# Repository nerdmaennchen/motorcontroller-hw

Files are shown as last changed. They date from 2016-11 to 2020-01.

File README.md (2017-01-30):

A somewhat easy to build two-layer PCB to controll BLDC-motors with.

The board is designed to have:
	- USB connection (every computer has a USB port but there are virtually no boards out there that offer a USB connection (without an FTDI in between))
	- up to 200W (tested) output power (theoretical -- when ignoring trace resistances -- maximum 900W)
	- digital Hall-Encoder interface
	- analog/absolute hall-encoder interface
	- BEMF measurement for hall-less operation
	- serial interface to cascade multiple BLDC-drivers over one USB interface
	- two PWM outputs for RC-servo motors
	- one connector to attach WS2812b LEDs
	- a layout that allows somewhat easy manufacturing by placing most parts on one layer (I've once built 15 pieces in 8h by hand soldering)
	
The board has four power domains:
	- internal 3.3V -- to power the microcontroller
	- USB-5V -- can power the internal 3.3V domain; protected from the external 5V domain with a diode thus protecting the USB-host from voltage spikes on the external 5V-domain
	- external 5V -- can power the internal 3.3V domain; powers the WS2812b LEDs and RC-servo motors

The board utilizes an STM32F401xx processor which is super nice to program, debug and due to its QFN48 footprint super easy to solder by hand -- as long as you have access to a rework station.
Software for the uC can be found here: https://github.com/nerdmaennchen/motorcontroller-uc-sw
Software for the USB-Host here: https://github.com/nerdmaennchen/motorcontroller-sw

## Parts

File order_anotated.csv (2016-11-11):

Qty | Value | Footprint
12 | 2.2uF | Capacitors_SMD:C_0603
12 | 1276-6592-1-ND
3 | 10nF | Capacitors_SMD:C_0603
3 | 1276-1921-1-ND
1 | 22nF | Capacitors_SMD:C_0603
1 | 490-3169-1-ND
3 | 100nF | Capacitors_SMD:C_0603
3 | 1276-1258-1-ND
1 | 4.7uF | Capacitors_SMD:C_0805
2 | 22pF | Capacitors_SMD:C_0603
2 | 1276-2227-1-ND
1 | status | LEDs:LED_0805
1 | 160-1434-1-ND
2 | D_Schottky | Diodes_SMD:SOD-323
2 | NSR0530HT1GOSCT-ND
4 | 3.3V | Diodes_SMD:SOD-323
4 | MM3Z3V3T1GOSCT-ND
1 | USB_OTG | Connect:USB_Micro-B
1 | 609-4618-1-ND
1 | CONN_01X03 | Terminal_Blocks:TerminalBlock_Pheonix_MPT-2.54mm_3pol
1 | ED10562-ND
1 | CON_PWR_BRD | Terminal_Blocks:TerminalBlock_Pheonix_MPT-2.54mm_4pol
1 | ED10563-ND
1 | CON_HALL | Terminal_Blocks:TerminalBlock_Pheonix_MPT-2.54mm_5pol
1 | ED10564-ND
6 | Q_NMOS_DGS | BLDC:SOT1210
6 | 568-13008-1-ND
1 | 2N7002 | TO_SOT_Packages_SMD:SOT-23
1 | 2N7002ECT-ND
1 | 330 | Resistors_SMD:R_0603
1 | 311-330GRCT-ND
4 | 10kR | Resistors_SMD:R_0603
4 | 311-10KGRCT-ND
1 | 1R | Resistors_SMD:R_0603
1 | 1276-4991-1-ND
6 | 10R | Resistors_SMD:R_0603
6 | 311-10KGRCT-ND
1 | 0R/50kR | Resistors_SMD:R_0603
1 | NA/50kR | Resistors_SMD:R_0603
1 | 311-47KGRCT-ND
2 | .01 | Resistors_SMD:R_1210
2 | 1276-6160-1-ND
1 | 33k | Resistors_SMD:R_Array_Concave_4x0603
1 | 742C083333JPCT-ND
1 | 1k | Resistors_SMD:R_Array_Concave_4x0603
1 | 742C083102JPCT-ND
1 | 10k | Resistors_SMD:R_Array_Concave_4x0603
1 | 742C083103JPCT-ND
1 | STM32F401CBUx | Housings_DFN_QFN:QFN-48-1EP_7x7mm_Pitch0.5mm
1 | LD1117S33TR | TO_SOT_Packages_SMD:SOT-223
1 | 497-1242-1-ND
1 | DRV8303 | BLDC:SOIC-48
1 | 296-40070-1-ND
1 | Crystal | Crystals:Crystal_SMD_5032_2Pads
1 | 535-10630-1-ND
Title
Date
Generated | Di 08 Nov 2016 14:40:50 CET
Total Parts | 76
Total Unique Parts | 37

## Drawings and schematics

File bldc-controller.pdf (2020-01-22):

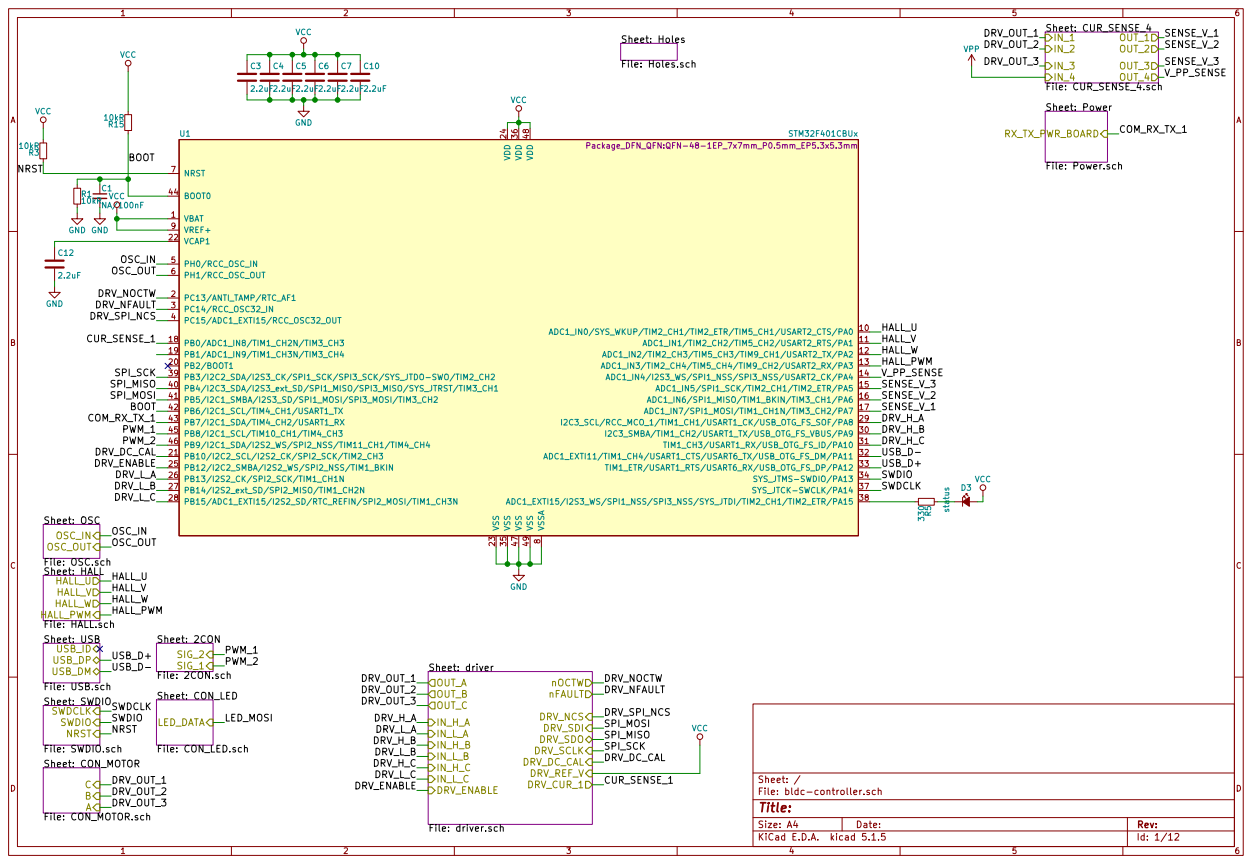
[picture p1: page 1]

Sheet: Holes File: Holes.sch Sheet: OSC

Sheet: Power File: Power.sch RX_TX_PWR_BOARD

Sheet: driver File: driver.sch OUT_A

SWDCLK SWDIO NRST

LED_DATA

Id: 1/12 Title: File: bldc-controller.sch Sheet: /

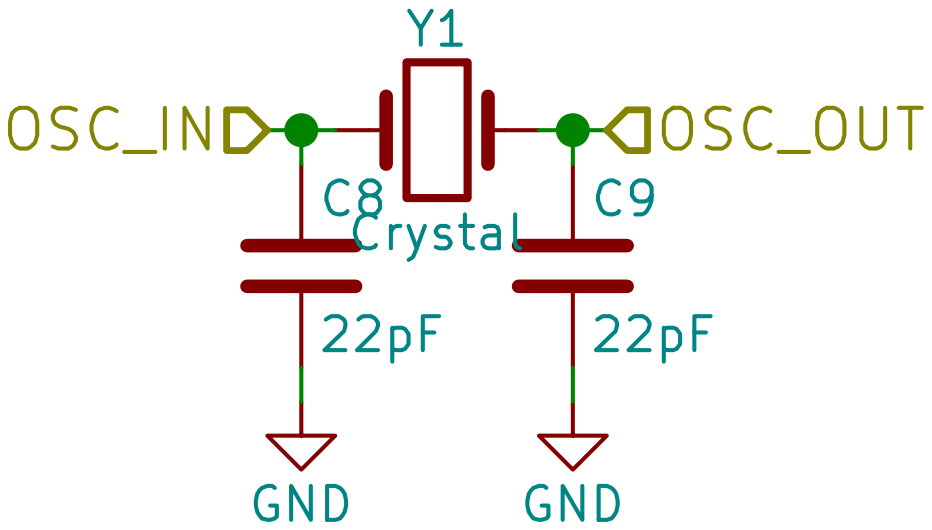
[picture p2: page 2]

Id: 2/12 Title: File: OSC.sch Sheet: /OSC/

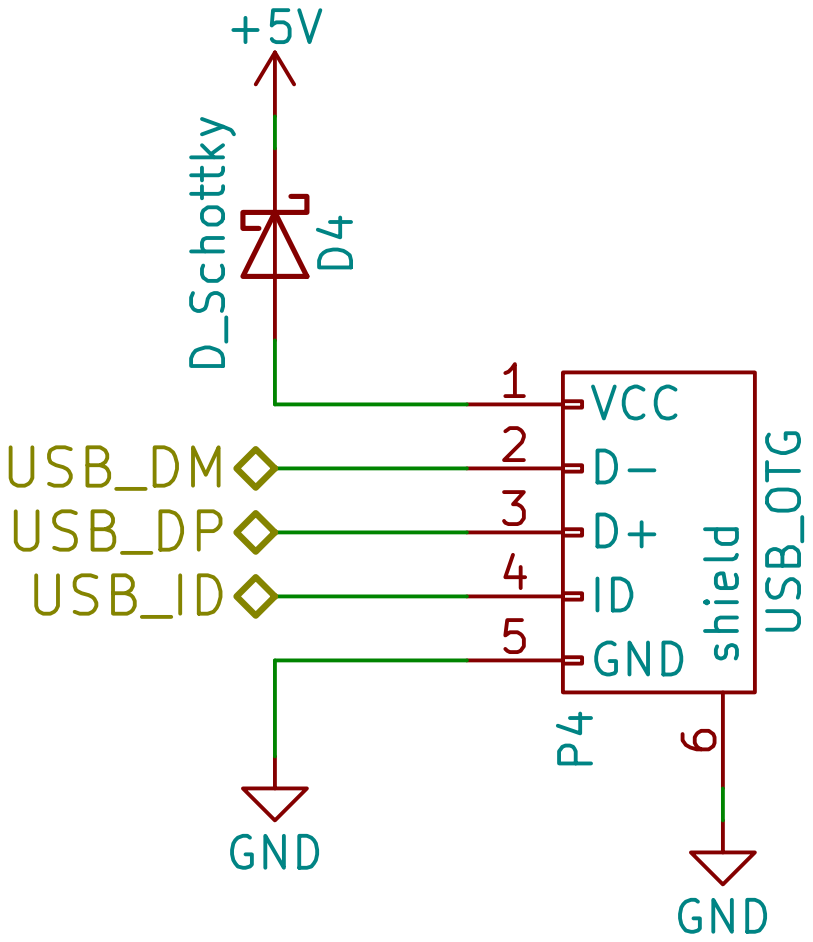
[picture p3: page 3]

Id: 3/12 Title: DreErolf File: USB.sch Sheet: /USB/ +5V

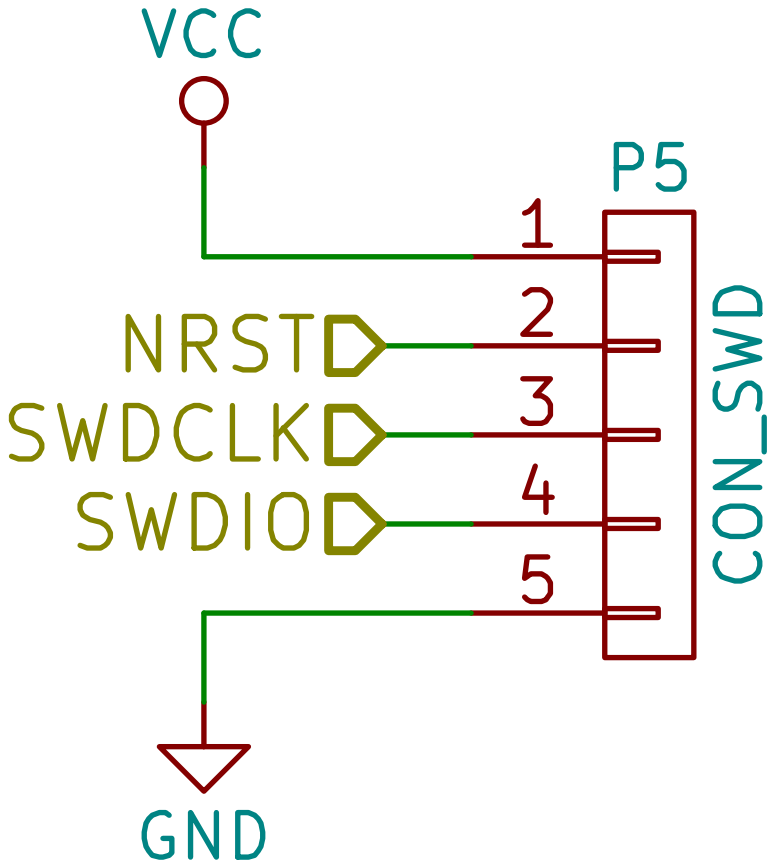
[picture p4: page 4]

Id: 4/12 Title: DreErolf File: SWDIO.sch Sheet: /SWDIO/ GND

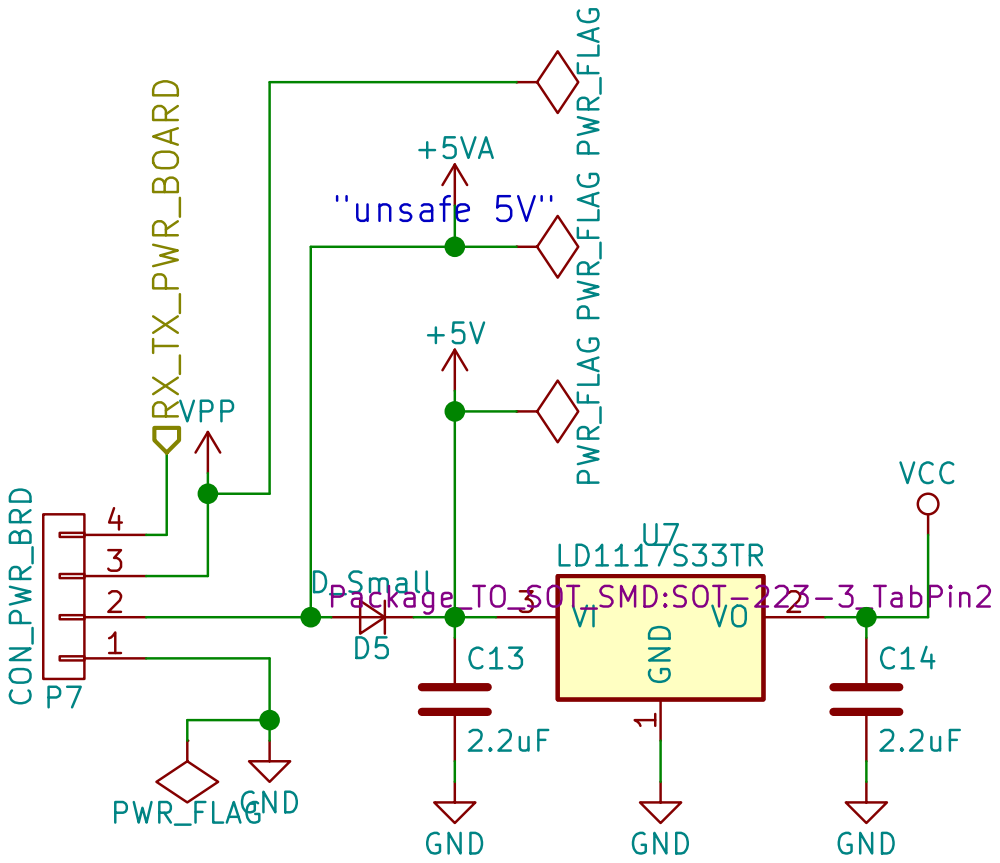
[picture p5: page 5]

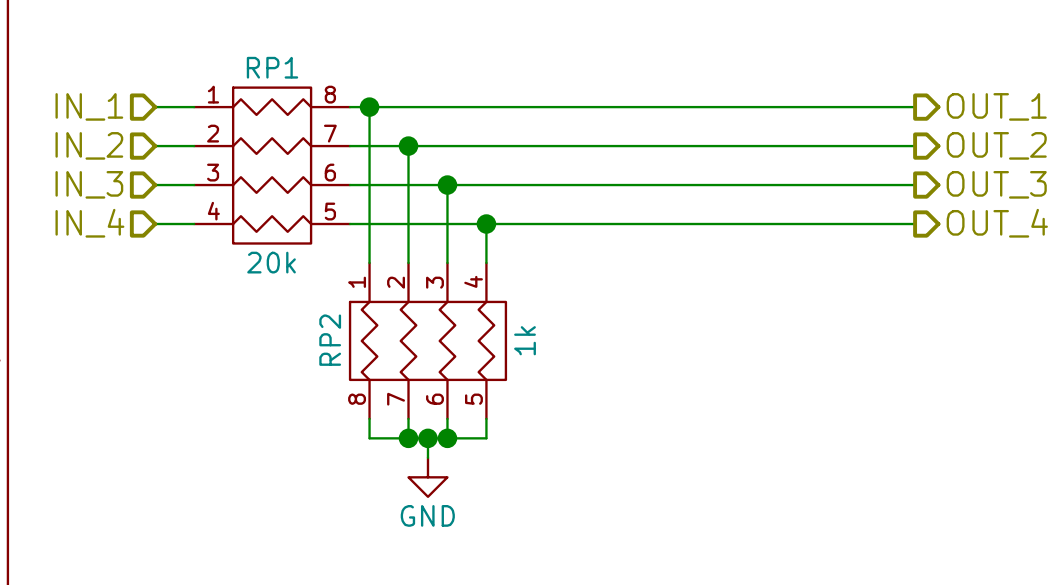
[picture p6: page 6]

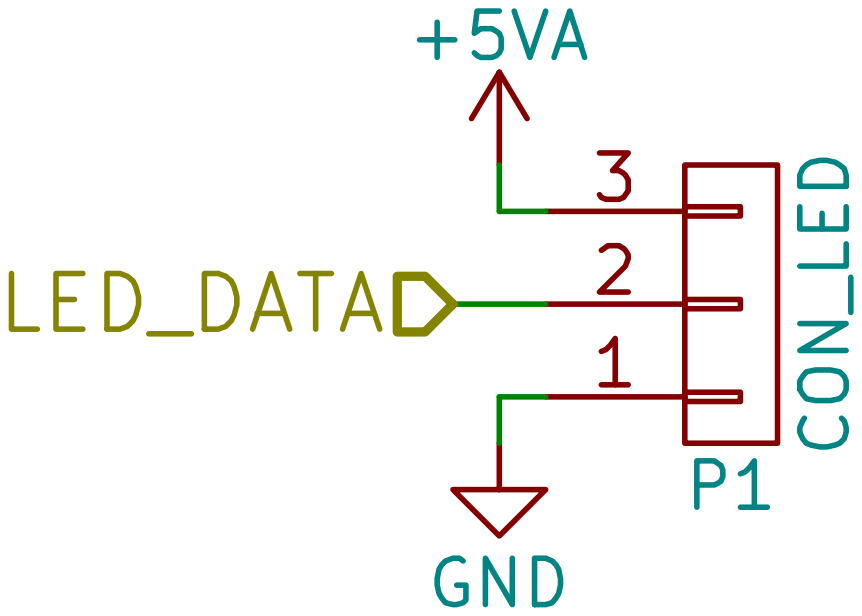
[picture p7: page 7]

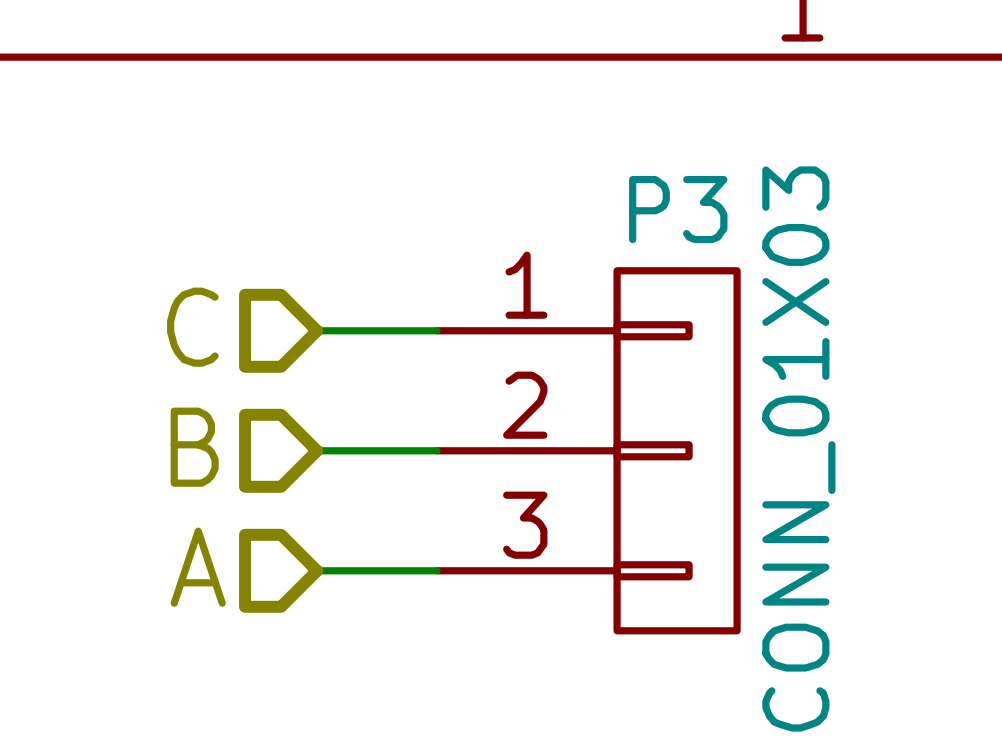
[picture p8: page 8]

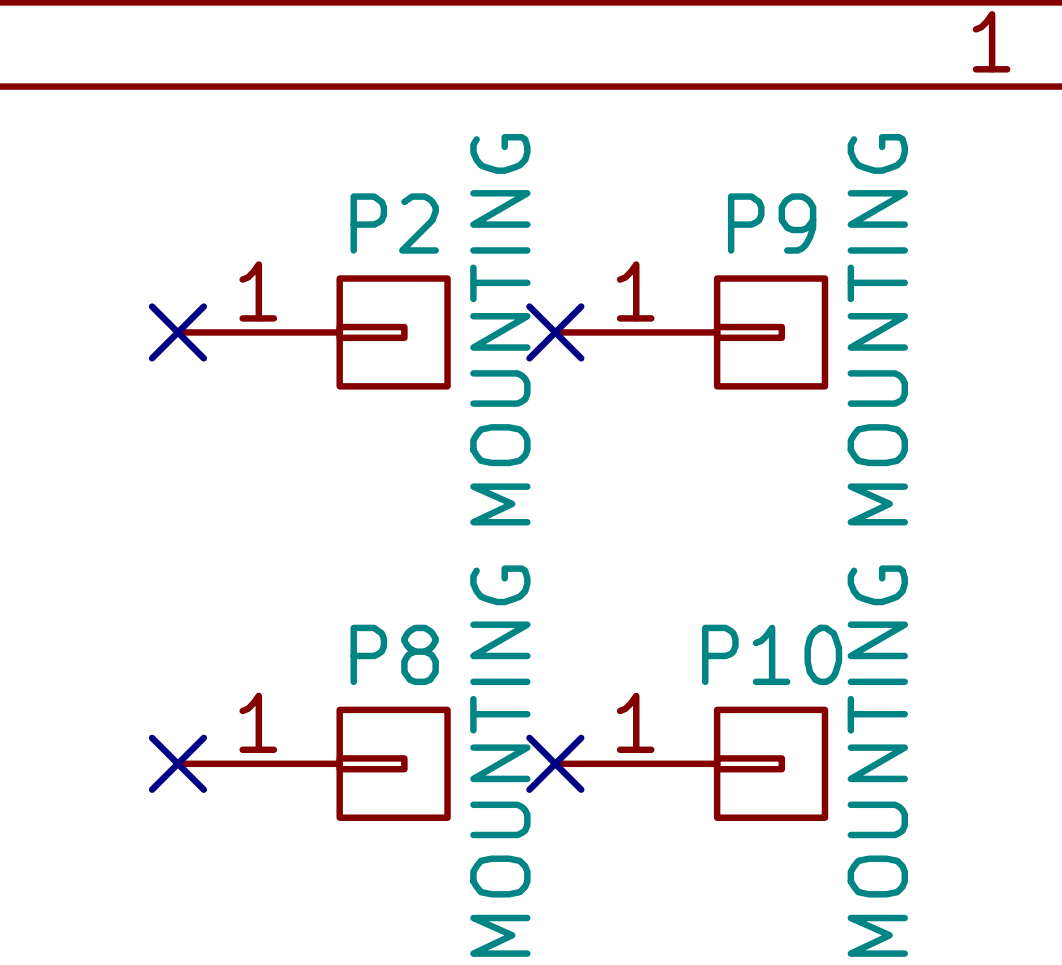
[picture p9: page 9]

Id: 9/12 Title: File: Holes.sch Sheet: /Holes/ 1 P2 MOUNTING 1 P9 MOUNTING 1 P8 MOUNTING 1 P10 MOUNTING

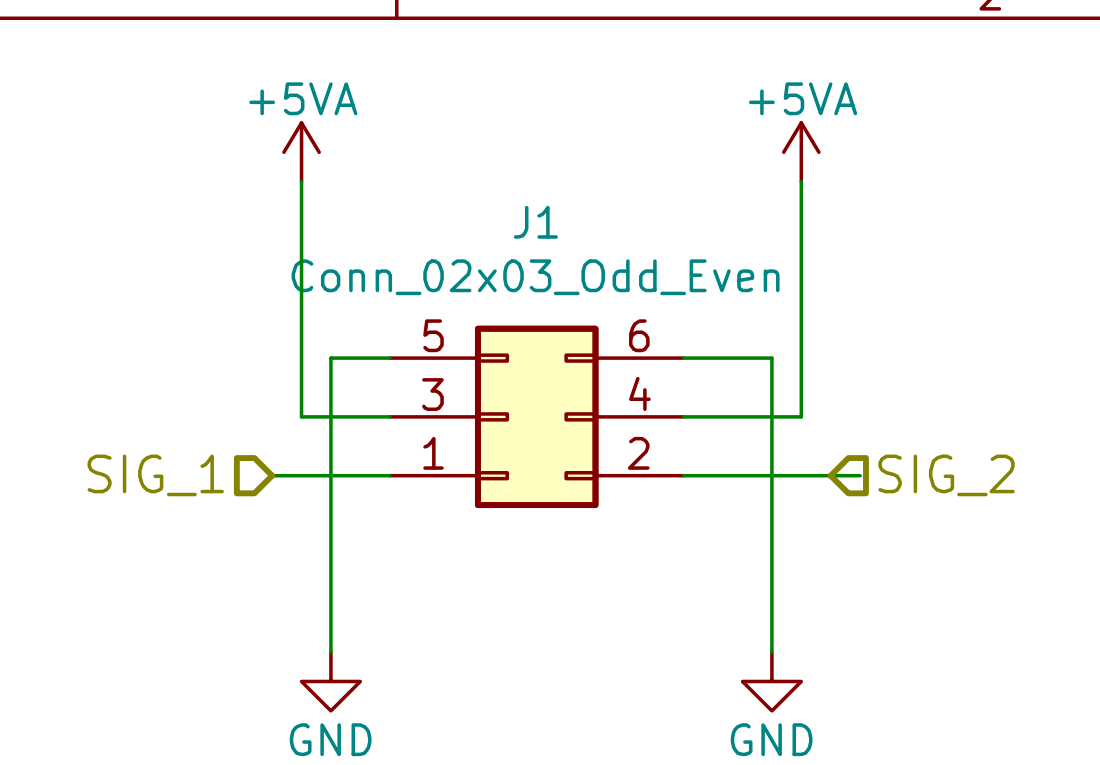
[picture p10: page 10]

Id: 10/12 Title: File: 2CON.sch Sheet: /2CON/

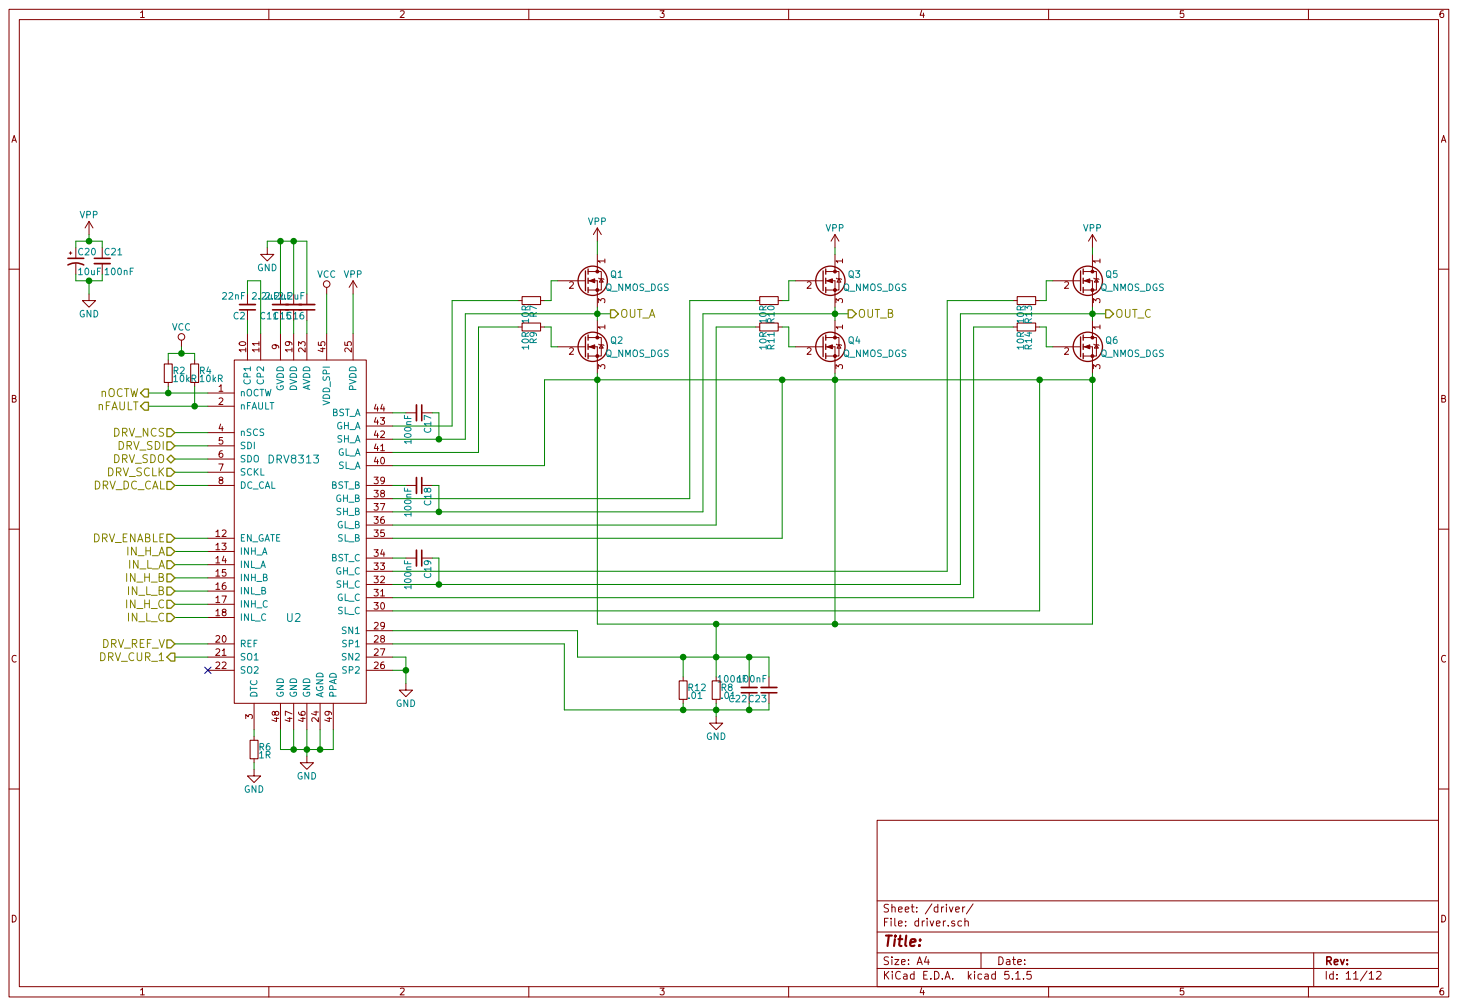
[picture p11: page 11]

Id: 11/12 Title: File: driver.sch Sheet: /driver/

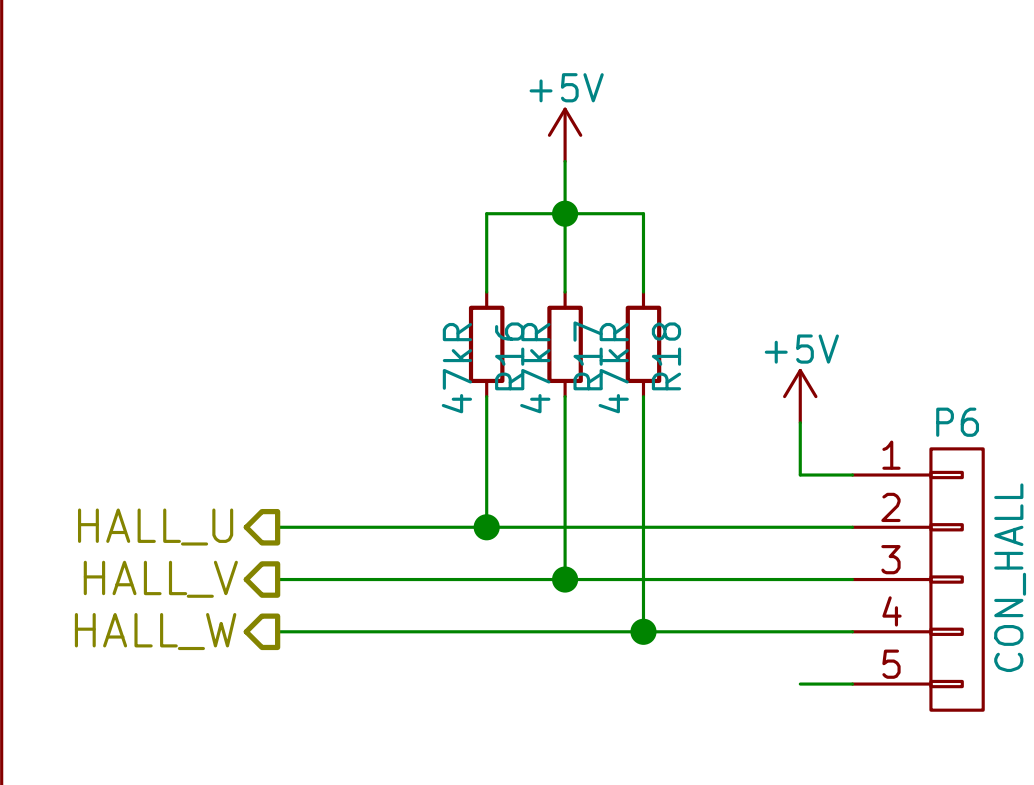
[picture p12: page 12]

Id: 12/12 Title: File: HALL.sch Sheet: /HALL/

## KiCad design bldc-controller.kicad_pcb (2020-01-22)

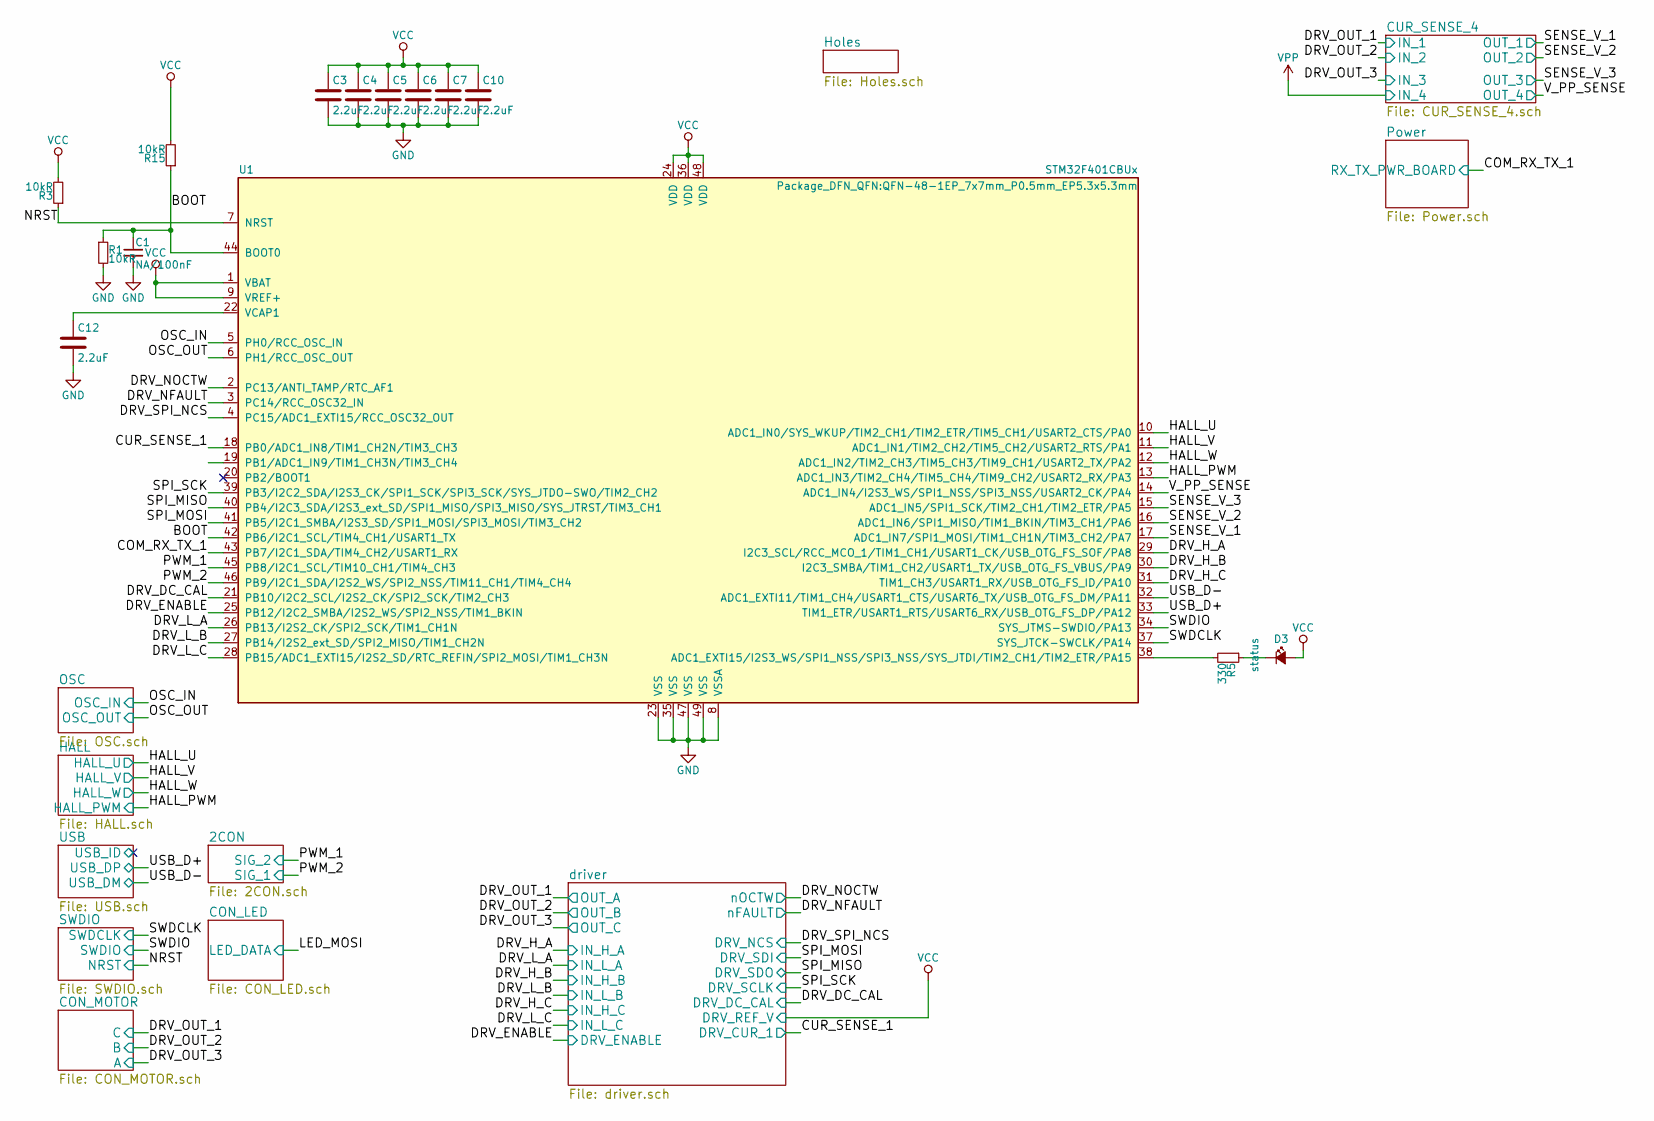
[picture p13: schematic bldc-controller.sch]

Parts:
C1: NA/100nF; C_0603_1608Metric
C3, C4, C5, C6, C7, C10, C12: 2.2uF; C_0603_1608Metric
D3: status; LED_0805_2012Metric
R1, R3, R15: 10kR; R_0603_1608Metric
R5: 330; R_0603_1608Metric
U1: STM32F401CBUx; QFN-48-1EP_7x7mm_P0.5mm_EP5.3x5.3mm

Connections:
/BOOT: C1.1, R1.1, R15.1, U1.42 (PB6/I2C1_SCL/TIM4_CH1/USART1_TX), U1.44 (BOOT0)
/COM_RX_TX_1: U1.43 (PB7/I2C1_SDA/TIM4_CH2/USART1_RX); also elsewhere on the board
/CUR_SENSE_1: U1.18 (PB0/ADC1_IN8/TIM1_CH2N/TIM3_CH3); also elsewhere on the board
/DRV_DC_CAL: U1.21 (PB10/I2C2_SCL/I2S2_CK/SPI2_SCK/TIM2_CH3); also elsewhere on the board
/DRV_ENABLE: U1.25 (PB12/I2C2_SMBA/I2S2_WS/SPI2_NSS/TIM1_BK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); also elsewhere on the board
/DRV_H_A: U1.29 (I2C3_SCL/RCC_MCO_1/TIM1_CH1/USART1_CK/U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); also elsewhere on the board
/DRV_H_B: U1.30 (I2C3_SMBA/TIM1_CH2/USART1_TX/USB_OTG_FS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); also elsewhere on the board
/DRV_H_C: U1.31 (TIM1_CH3/USART1_RX/USB_OTG_FS_ID/PA10); also elsewhere on the board
/DRV_L_A: U1.26 (PB13/I2S2_CK/SPI2_SCK/TIM1_CH1N); also elsewhere on the board
/DRV_L_B: U1.27 (PB14/I2S2_ext_SD/SPI2_MISO/TIM1_CH2N); also elsewhere on the board
/DRV_L_C: U1.28 (PB15/ADC1_EXTI15/I2S2_SD/RTC_REFIN/SPI2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); also elsewhere on the board
/DRV_NFAULT: U1.3 (PC14/RCC_OSC32_IN); also elsewhere on the board
/DRV_NOCTW: U1.2 (PC13/ANTI_TAMP/RTC_AF1); also elsewhere on the board
/DRV_SPI_NCS: U1.4 (PC15/ADC1_EXTI15/RCC_OSC32_OUT); also elsewhere on the board
/HALL_U: U1.10 (ADC1_IN0/SYS_WKUP/TIM2_CH1/TIM2_ETR/TIM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); also elsewhere on the board
/HALL_V: U1.11 (ADC1_IN1/TIM2_CH2/TIM5_CH2/USART2_RTS/P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); also elsewhere on the board
/HALL_W: U1.12 (ADC1_IN2/TIM2_CH3/TIM5_CH3/TIM9_CH1/USA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); also elsewhere on the board
/NRST: R3.1, U1.7 (NRST); also elsewhere on the board
/OSC_IN: U1.5 (PH0/RCC_OSC_IN); also elsewhere on the board
/OSC_OUT: U1.6 (PH1/RCC_OSC_OUT); also elsewhere on the board
/PWM_1: U1.45 (PB8/I2C1_SCL/TIM10_CH1/TIM4_CH3); also elsewhere on the board
/PWM_2: U1.46 (PB9/I2C1_SDA/I2S2_WS/SPI2_NSS/TIM11_CH1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); also elsewhere on the board
/SENSE_V_1: U1.17 (ADC1_IN7/SPI1_MOSI/TIM1_CH1N/TIM3_CH2/P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); also elsewhere on the board
/SENSE_V_2: U1.16 (ADC1_IN6/SPI1_MISO/TIM1_BKIN/TIM3_CH1/P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); also elsewhere on the board
/SENSE_V_3: U1.15 (ADC1_IN5/SPI1_SCK/TIM2_CH1/TIM2_ETR/PA5); also elsewhere on the board
/SPI_MISO: U1.40 (PB4/I2C3_SDA/I2S3_ext_SD/SPI1_MISO/SPI3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); also elsewhere on the board
/SPI_MOSI: U1.41 (PB5/I2C1_SMBA/I2S3_SD/SPI1_MOSI/SPI3_MO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); also elsewhere on the board
/SPI_SCK: U1.39 (PB3/I2C2_SDA/I2S3_CK/SPI1_SCK/SPI3_SCK/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); also elsewhere on the board
/SWDCLK: U1.37 (SYS_JTCK-SWCLK/PA14); also elsewhere on the board
/SWDIO: U1.34 (SYS_JTMS-SWDIO/PA13); also elsewhere on the board
/USB_D+: U1.33 (TIM1_ETR/USART1_RTS/USART6_RX/USB_OTG_F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); also elsewhere on the board
/USB_D-: U1.32 (ADC1_EXTI11/TIM1_CH4/USART1_CTS/USART6_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); also elsewhere on the board
/V_PP_SENSE: U1.14 (ADC1_IN4/I2S3_WS/SPI1_NSS/SPI3_NSS/USAR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); also elsewhere on the board
GND: C1.2, C3.2, C4.2, C5.2, C6.2, C7.2, C10.2, C12.2, R1.2, U1.8 (VSSA), U1.23 (VSS), U1.35 (VSS), U1.47 (VSS), U1.49 (VSS); also elsewhere on the board
unnamed: C12.1, U1.22 (VCAP1)
unnamed: D3.1 (K), R5.1
unnamed: R5.2, U1.38 (ADC1_EXTI15/I2S3_WS/SPI1_NSS/SPI3_NSS/S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)
VCC: C3.1, C4.1, C5.1, C6.1, C7.1, C10.1, D3.2 (A), R3.2, R15.2, U1.1 (VBAT), U1.9 (VREF+), U1.24 (VDD), U1.36 (VDD), U1.48 (VDD); also elsewhere on the board

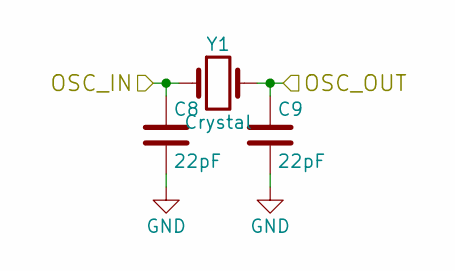
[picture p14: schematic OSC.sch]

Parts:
C8, C9: 22pF; C_0603_1608Metric
Y1: Crystal; Crystal_SMD_5032-2Pin_5.0x3.2mm

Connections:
/OSC_IN: C8.1, Y1.1; also elsewhere on the board
/OSC_OUT: C9.1, Y1.2; also elsewhere on the board
GND: C8.2, C9.2; also elsewhere on the board

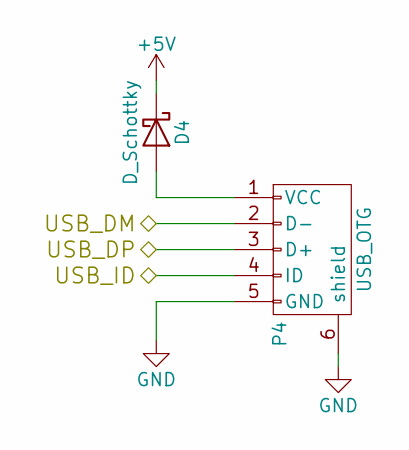
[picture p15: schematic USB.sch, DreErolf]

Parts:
D4: D_Schottky; D_SOD-323
P4: USB_OTG; USB_Micro-B_Molex_47346-0001

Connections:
+5V: D4.1 (K); also elsewhere on the board
/USB_D+: P4.3 (D+); also elsewhere on the board
/USB_D-: P4.2 (D-); also elsewhere on the board
GND: P4.5 (GND), P4.6 (shield); also elsewhere on the board
unnamed: D4.2 (A), P4.1 (VCC)

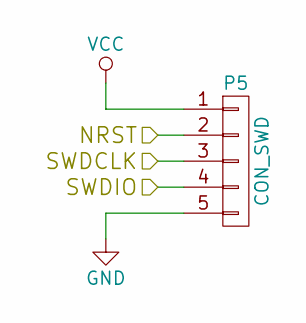
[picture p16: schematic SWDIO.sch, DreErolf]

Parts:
P5: CON_SWD; PinHeader_1x05_P2.54mm_Vertical

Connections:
/NRST: P5.2; also elsewhere on the board
/SWDCLK: P5.3; also elsewhere on the board
/SWDIO: P5.4; also elsewhere on the board
GND: P5.5; also elsewhere on the board
VCC: P5.1; also elsewhere on the board

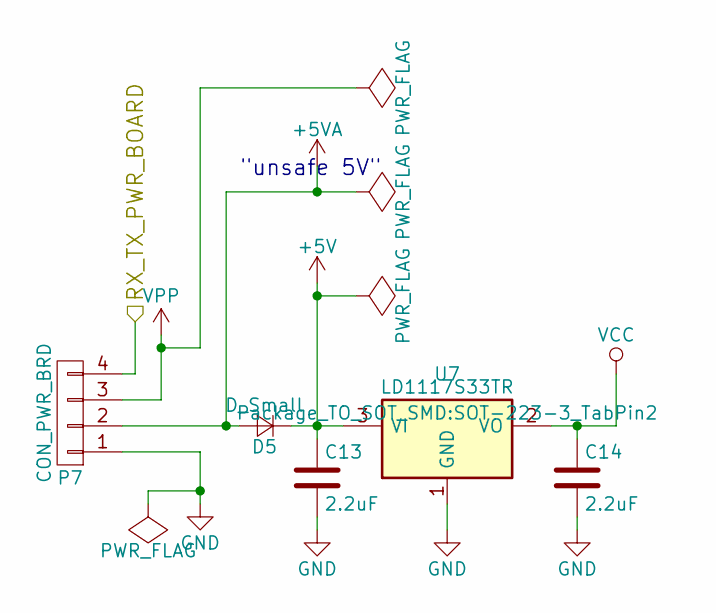
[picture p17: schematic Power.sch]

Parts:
C13, C14: 2.2uF; C_0603_1608Metric
D5: D_Small; D_SOD-323
P7: CON_PWR_BRD; PinHeader_1x04_P2.54mm_Vertical
U7: LD1117S33TR; SOT-223-3_TabPin2

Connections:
+5V: C13.1, D5.1 (K), U7.3 (VI); also elsewhere on the board
+5VA: D5.2 (A), P7.2; also elsewhere on the board
/COM_RX_TX_1: P7.4; also elsewhere on the board
GND: C13.2, C14.2, P7.1, U7.1 (GND); also elsewhere on the board
VCC: C14.1, U7.2 (VO); also elsewhere on the board
VPP: P7.3; also elsewhere on the board

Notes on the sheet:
"unsafe 5V"

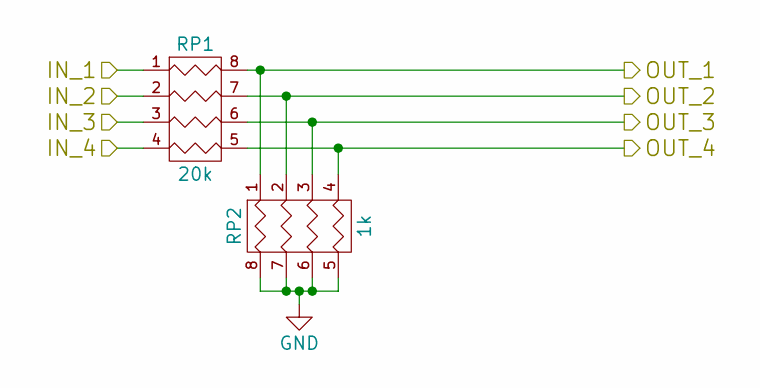
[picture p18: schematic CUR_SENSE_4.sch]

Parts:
RP1: 20k; R_Array_Concave_4x0603
RP2: 1k; R_Array_Concave_4x0603

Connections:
/DRV_OUT_1: RP1.1; also elsewhere on the board
/DRV_OUT_2: RP1.2; also elsewhere on the board
/DRV_OUT_3: RP1.3; also elsewhere on the board
/SENSE_V_1: RP1.8 (R1), RP2.1; also elsewhere on the board
/SENSE_V_2: RP1.7 (R2), RP2.2; also elsewhere on the board
/SENSE_V_3: RP1.6 (R3), RP2.3; also elsewhere on the board
/V_PP_SENSE: RP1.5 (R4), RP2.4; also elsewhere on the board
GND: RP2.5 (R4), RP2.6 (R3), RP2.7 (R2), RP2.8 (R1); also elsewhere on the board
VPP: RP1.4; also elsewhere on the board

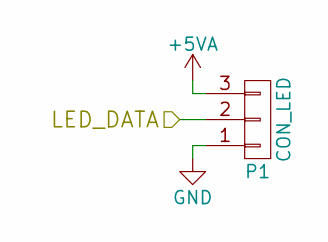
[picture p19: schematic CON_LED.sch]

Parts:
P1: CON_LED; PinHeader_1x03_P2.54mm_Vertical

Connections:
+5VA: P1.3; also elsewhere on the board
GND: P1.1; also elsewhere on the board

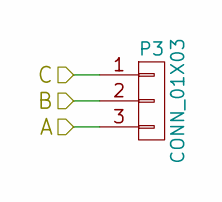
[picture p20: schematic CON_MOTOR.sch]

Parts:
P3: CONN_01X03; PinHeader_1x03_P2.54mm_Horizontal

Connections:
/DRV_OUT_1: P3.1; also elsewhere on the board
/DRV_OUT_2: P3.2; also elsewhere on the board
/DRV_OUT_3: P3.3; also elsewhere on the board

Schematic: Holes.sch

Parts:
P2, P8, P9, P10: MOUNTING; 1pin

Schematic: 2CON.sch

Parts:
J1: Conn_02x03_Odd_Even; PinHeader_2x03_P2.00mm_Horizontal

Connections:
+5VA: J1.3, J1.4; also elsewhere on the board
/PWM_1: J1.2; also elsewhere on the board
/PWM_2: J1.1; also elsewhere on the board
GND: J1.5, J1.6; also elsewhere on the board

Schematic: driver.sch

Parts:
C2: 22nF; C_0603_1608Metric
C11, C15, C16: 2.2uF; C_0603_1608Metric
C17, C18, C19, C21, C22, C23: 100nF; C_0603_1608Metric
C20: 10uF; CP_Elec_5x3
Q1, Q2, Q3, Q4, Q5, Q6: Q_NMOS_DGS; SOT1210
R2, R4: 10kR; R_0603_1608Metric
R6: 1R; R_0603_1608Metric
R7, R9, R10, R11, R13, R14: 10R; R_0603_1608Metric
R8, R12: .01; R_1206_3216Metric
U2: DRV8313; SOIC-48

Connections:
/CUR_SENSE_1: U2.21 (SO1); also elsewhere on the board
/DRV_DC_CAL: U2.8 (DC_CAL); also elsewhere on the board
/DRV_ENABLE: U2.12 (EN_GATE); also elsewhere on the board
/DRV_H_A: U2.13 (INH_A); also elsewhere on the board
/DRV_H_B: U2.15 (INH_B); also elsewhere on the board
/DRV_H_C: U2.17 (INH_C); also elsewhere on the board
/DRV_L_A: U2.14 (INL_A); also elsewhere on the board
/DRV_L_B: U2.16 (INL_B); also elsewhere on the board
/DRV_L_C: U2.18 (INL_C); also elsewhere on the board
/DRV_NFAULT: R4.2, U2.2 (nFAULT); also elsewhere on the board
/DRV_NOCTW: R2.2, U2.1 (nOCTW); also elsewhere on the board
/DRV_OUT_1: C17.1, Q1.3 (S), Q2.1 (D), U2.42 (SH_A); also elsewhere on the board
/DRV_OUT_2: C18.1, Q3.3 (S), Q4.1 (D), U2.37 (SH_B); also elsewhere on the board
/DRV_OUT_3: C19.1, Q5.3 (S), Q6.1 (D), U2.32 (SH_C); also elsewhere on the board
/DRV_SPI_NCS: U2.4 (nSCS); also elsewhere on the board
/SPI_MISO: U2.6 (SDO); also elsewhere on the board
/SPI_MOSI: U2.5 (SDI); also elsewhere on the board
/SPI_SCK: U2.7 (SCKL); also elsewhere on the board
GND: C11.2, C15.2, C16.2, C20.2, C21.2, C22.1, C23.1, R6.2, R8.2, R12.2, U2.24 (AGND), U2.26 (SP2), U2.27 (SN2), U2.28 (SP1), U2.46 (GND), U2.47 (GND), U2.48 (GND), U2.49 (PPAD); also elsewhere on the board
unnamed: C2.1, U2.10 (CP1)
unnamed: C2.2, U2.11 (CP2)
unnamed: C11.1, U2.9 (GVDD)
unnamed: C15.1, U2.19 (DVDD)
unnamed: C16.1, U2.23 (AVDD)
unnamed: C17.2, U2.44 (BST_A)
unnamed: C18.2, U2.39 (BST_B)
unnamed: C19.2, U2.34 (BST_C)
unnamed: C22.2, C23.2, Q2.3 (S), Q4.3 (S), Q6.3 (S), R8.1, R12.1, U2.29 (SN1), U2.30 (SL_C), U2.35 (SL_B), U2.40 (SL_A)
unnamed: Q1.2 (G), R7.1
unnamed: Q2.2 (G), R9.1
unnamed: Q3.2 (G), R10.1
unnamed: Q4.2 (G), R11.1
unnamed: Q5.2 (G), R13.1
unnamed: Q6.2 (G), R14.1
unnamed: R6.1, U2.3 (DTC)
unnamed: R7.2, U2.43 (GH_A)
unnamed: R9.2, U2.41 (GL_A)
unnamed: R10.2, U2.38 (GH_B)
unnamed: R11.2, U2.36 (GL_B)
unnamed: R13.2, U2.33 (GH_C)
unnamed: R14.2, U2.31 (GL_C)
VCC: R2.1, R4.1, U2.20 (REF), U2.45 (VDD_SPI); also elsewhere on the board
VPP: C20.1, C21.1, Q1.1 (D), Q3.1 (D), Q5.1 (D), U2.25 (PVDD); also elsewhere on the board

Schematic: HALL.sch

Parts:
P6: CON_HALL; PinHeader_1x05_P2.54mm_Horizontal
R16, R17, R18: 47kR; R_0603_1608Metric

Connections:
+5V: P6.1, R16.2, R17.2, R18.2; also elsewhere on the board
/HALL_U: P6.2, R16.1; also elsewhere on the board
/HALL_V: P6.3, R17.1; also elsewhere on the board
/HALL_W: P6.4, R18.1; also elsewhere on the board

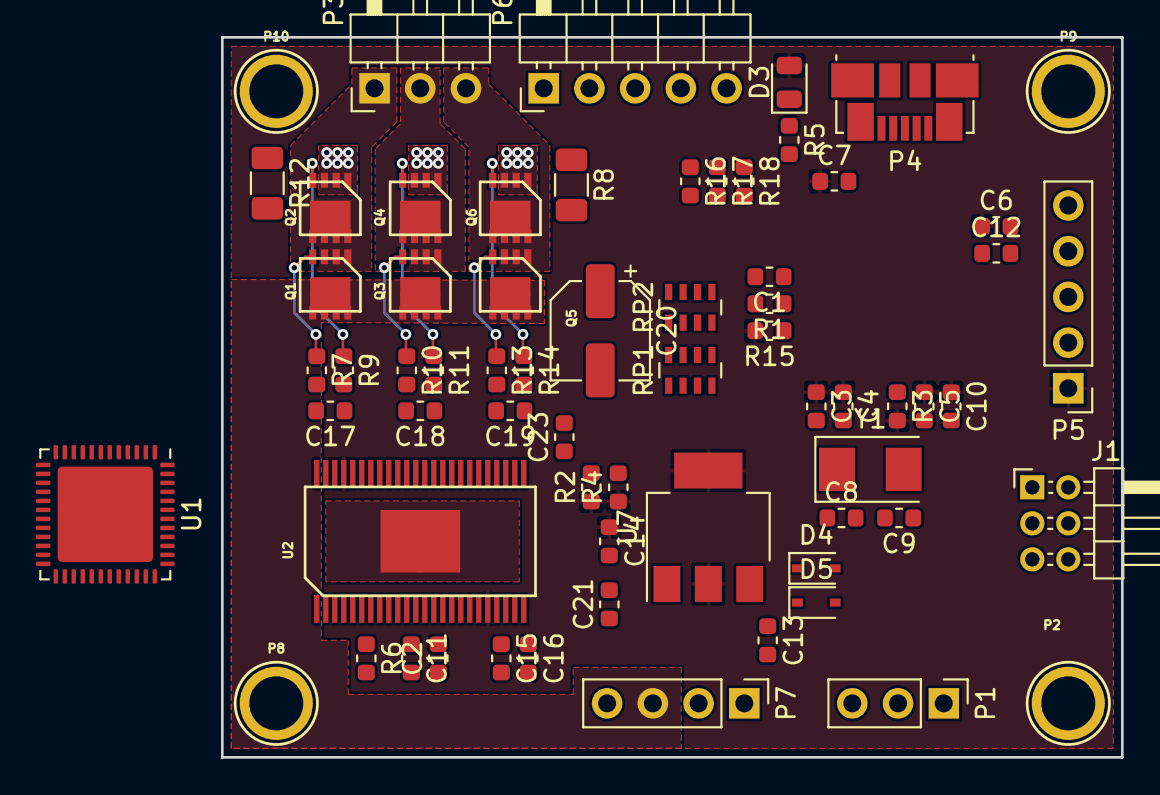
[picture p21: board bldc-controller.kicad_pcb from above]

Board: 2 copper layers, 50.0 x 40.0 mm, 67 parts (1 on the bottom side), 67 nets.

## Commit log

2016-09-08 updated some stuff and added some more docu
    [Power.sch, bldc-controller.csv, bldc-controller.kicad_pcb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]
2016-10-20 updated stuff
    [2CON.sch, CON_LED.sch, CON_MOTOR.sch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]
2016-10-24 i think im good with the schematics
    [CUR_SENSE_4.sch, HALL.sch, USB.sch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]
2016-10-25 changed the maximum outpul voltage of the RC-Filter to VPP
    [HALL.sch, bldc-controller.sch]
2016-10-31 routed... at least for now
    [2CON.sch, CON_LED.sch, CON_MOTOR.sch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]
2016-10-31 some sugar
    [bldc-controller.kicad_pcb]
2016-11-01 well... actually we dont need those thwo parts since the bootloader can be entered from flash software
    [bldc-controller.kicad_pcb, bldc-controller.sch]
2016-11-01 even though Im pretty sure that resistor is actually not needed Id like to play safe and have it anyway
    [bldc-controller.kicad_pcb, bldc-controller.sch]
2016-11-07 corrected order version
    [bldc-controller.kicad_pcb]
2016-11-11 changed that capacitor to a more reasonable value
    [driver.sch]
2016-11-11 small update
    [order.csv, order_anotated.csv]
2016-12-22 Create README.txt
    Bitte lesen und antworten!
2017-01-11 some sugar coating and updated gerbers
    [CON_LED.sch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]
2017-01-30 updated the readme -- this is _not_ a substitute to email me haha --
    [bldc-controller.kicad_pcb]
2017-03-23 we dont need those files
    [bldc-controller-B.Cu.gbr, bldc-controller-B.SilkS.gbr, bldc-controller-Edge.Cuts.gbr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]
2017-05-07 dropped those obsolete files
    [CON_LIDAR.sch, IMU.sch]
2020-01-22 long forgotten commit of something I did half a year ago -.-
    [2CON.sch, CON_LED.sch, CON_MOTOR.sch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]
